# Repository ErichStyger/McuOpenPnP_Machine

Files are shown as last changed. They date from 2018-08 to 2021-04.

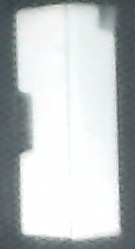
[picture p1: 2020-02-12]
CHM36VA_OpenPnP/V2/org.openpnp.machine.reference.feeder.ReferenceDragFeeder.Vision/tmpl_2714184057134874055.png

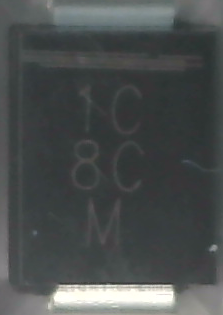
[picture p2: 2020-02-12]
CHM36VA_OpenPnP/V2/org.openpnp.machine.reference.feeder.ReferenceDragFeeder.Vision/tmpl_781869377021545644.png

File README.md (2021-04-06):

# McuOpenPnP_Machine
Repository for the McuOnEclipse OpenPnP machine.

The AutoFeeder is a contribution from Simon Huber (https://github.com/Scavenger18/RepoPNP) (many thanks!).

You can find overview videos about it on YouTube:
- Pick&Place Maschine Overview (Embedded Computing Conference 2018 Talk): https://youtu.be/OPd62hStLSc
- Pick&Place OpenPnP Overview (Embedded Computing Conference 2018 Talk): https://youtu.be/8GyD9tZBJVQ
- Placing SMD Resistors with OpenPnP Pick&Place machine: https://youtu.be/lebx-vkmo2o
- OpenPnP Pick&Place Component Iteration: https://youtu.be/lf4krekVuLk
- OpenPnP and Board Fiducials: https://youtu.be/fgSJTeFeqYE
- Nozzle Change with OpenPnP: https://youtu.be/CIzX5zvgmOw
- CHM-T32VA OpenPnP Conversion: https://mcuoneclipse.com/2020/05/03/retrofitting-a-charmhigh-chm-t36va-machine-with-openpnp/

And check out my blog articles on OpenPnP: https://mcuoneclipse.com/tag/openpnp/

Enjoy!

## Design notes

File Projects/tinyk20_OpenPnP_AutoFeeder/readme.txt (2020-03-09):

readme.txt
----------
Project for an OpenPnP Feeder using Kinetis Design Studio V3.2.0.

Links:
https://mcuoneclipse.com/2018/05/05/sneak-preview-diy-smt-pick-place-machine-with-openpnp/
https://mcuoneclipse.com/2018/06/26/building-a-diy-smt-pickplace-machine-with-openpnp/
https://mcuoneclipse.com/2018/06/03/embedded-computing-conference-2018-pickplace-overview-video/
https://mcuoneclipse.com/2018/03/18/3d-printed-smt-cut-tape-holder/
https://mcuoneclipse.com/2019/11/26/openpnp-solder-paste-dispensing-video/
https://mcuoneclipse.com/2019/08/15/openpnp-solder-dispenser-sneak-preview/

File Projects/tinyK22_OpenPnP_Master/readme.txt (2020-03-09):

readme.txt
----------

This project implements a sub driver for an OpenPnP (www.openpnp.org) pick and place machine, using Kinetis Design Studio 3.2.0.

USB, RTT and UART (over USB with AS1) are used to communicate with the host.
AS2 is used as UART connection to the OpenPnP feeders.

Links:
https://mcuoneclipse.com/2018/05/05/sneak-preview-diy-smt-pick-place-machine-with-openpnp/
https://mcuoneclipse.com/2018/06/26/building-a-diy-smt-pickplace-machine-with-openpnp/
https://mcuoneclipse.com/2018/06/03/embedded-computing-conference-2018-pickplace-overview-video/
https://mcuoneclipse.com/2018/03/18/3d-printed-smt-cut-tape-holder/
https://mcuoneclipse.com/2019/11/26/openpnp-solder-paste-dispensing-video/
https://mcuoneclipse.com/2019/08/15/openpnp-solder-dispenser-sneak-preview/

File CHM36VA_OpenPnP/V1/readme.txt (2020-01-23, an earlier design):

machine configuration files for the CHM36VA with OpenPnP.

Commands:

Defaults:
	COMMAND_CONFIRM_REGEX	
		^ok.*
	CONNECT_COMMAND
		G21 ; Set millimeters mode
		G90 ; Set absolute positioning mode
		M82 ; Set absolute mode for extruder
	HOME_COMMAND
		G28 ; Home all axes
	MOVE_TO_COMMAND
		G0 {X:X%.4f} {Y:Y%.4f} {Z:Z%.4f} {Rotation:E%.4f} F{FeedRate:%.0f} ; Send standard Gcode move
		M400 ; Wait for moves to complete before returning

VAC
	ACTUATE_BOOLEAN_COMMAND		M80{True:8}{False:9} ; M808/809

BLOW
	ACTUATE_BOOLEAN_COMMAND		M81{True:2}{False:3} ; M812/813

UPLED
	ACTUATE_BOOLEAN_COMMAND		M81{True:0}{False:1} ; M810/811
	ACTUATE_DOUBLE_COMMAND		M810 S{IntegerValue}

DOWNLED
	ACTUATE_BOOLEAN_COMMAND		M81{True:4}{False:5} ; M814/815
	ACTUATE_DOUBLE_COMMAND		M814 S{IntegerValue}		

CAMSW (not used any more)
	ACTUATE_BOOLEAN_COMMAND		M81{True:8}{False:9} ; M818/819	

RFEEDER
	ACTUATE_BOOLEAN_COMMAND		T3G92E0G0E5	

Head: N1 is left, N2 is right

H1:N1VSENSE	
	ACTUATOR_READ_COMMAND		M105 ; read temp
	ACTUATOR_READ_REGEX		^ok V1:(?<Value>\d+\.\d+) /0.0 @0 V2:(?<n2vsense>\d+\.\d+) /0.0 @0
H1:N2VSENSE
	ACTUATOR_READ_COMMAND		M105 ; read temp
	ACTUATOR_READ_REGEX		^ok V1:(?<n1vsense>\d+\.\d+) /0.0 @0 V2:(?<Value>\d+\.\d+) /0.0 @0

H1:N1VAC	N1 vaccuum on/off
	ACTUATE_BOOLEAN_COMMAND		M80{True:0}{False:1} ; M800/801

H1:N2VAC	N2 vaccuum on/off
	ACTUATE_BOOLEAN_COMMAND		M80{True:4}{False:5} ; M804/805

H1:DRAGPIN (caution: do not enable it for more than a second, otherwise it will be damaged!)
	ACTUATE_BOOLEAN_COMMAND		
		M81{True:6}{False:7} ; M816/817
		G4P50 ; 100ms delay to deploy/retract
	ACTUATOR_READ_COMMAND		M119 ; endstop status
	ACTUATOR_READ_REGEX		^X_min:\d Y_min:\d Z_min:\d pins- \(X\)P\d.\d+:\d \(Y\)P\d.\d+:\d \(Z\)P\d.\d+:\d \(Z\)P\d.\d+:(?<Value>\d)

H1:ZMIN
	ACTUATOR_READ_COMMAND		M119 ; endstop status
	ACTUATOR_READ_REGEX		^X_min:\d Y_min:\d Z_min:\d pins- \(X\)P\d.\d+:\d \(Y\)P\d.\d+:\d \(Z\)P\d.\d+:(?<Value>\d) \(Z\)P\d.\d+:\d

H1:LFEEDER
	ACTUATE_BOOLEAN_COMMAND		T2G92E0G0E5

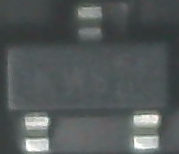
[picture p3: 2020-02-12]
CHM36VA_OpenPnP/V2/org.openpnp.machine.reference.feeder.ReferenceDragFeeder.Vision/tmpl_8623262849887002357.png

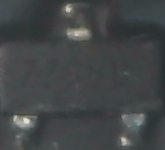
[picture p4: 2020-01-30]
CHM36VA_OpenPnP/V2/org.openpnp.machine.reference.feeder.ReferenceDragFeeder.Vision/tmpl_7061659952518420808.png

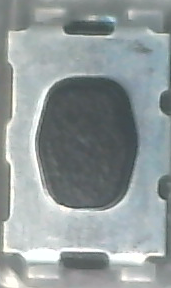
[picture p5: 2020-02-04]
CHM36VA_OpenPnP/V2/org.openpnp.machine.reference.feeder.ReferenceDragFeeder.Vision/tmpl_8939954195139066823.png

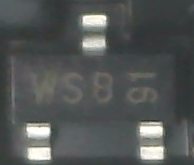
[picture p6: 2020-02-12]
CHM36VA_OpenPnP/V2/org.openpnp.machine.reference.feeder.ReferenceDragFeeder.Vision/tmpl_3286097203758662613.png

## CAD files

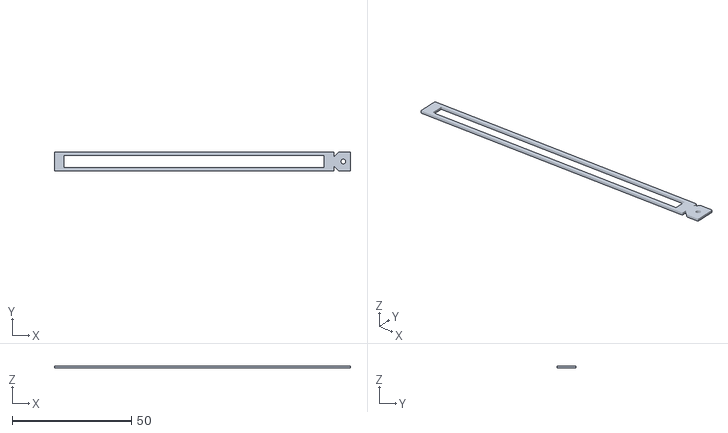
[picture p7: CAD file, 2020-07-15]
3D/StripFeeders.stl
124.0 x 8.00 x 1.00

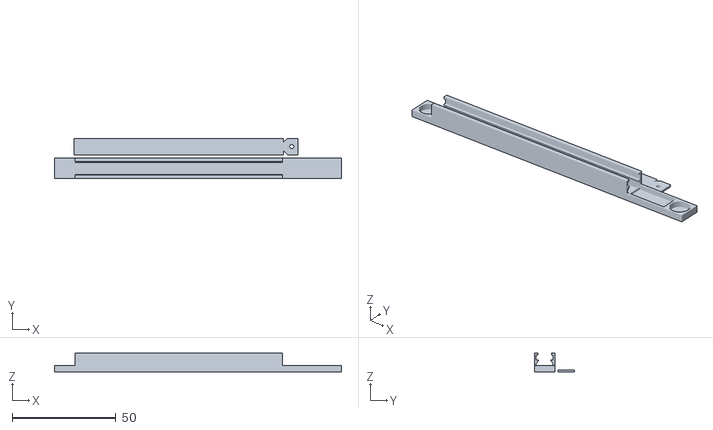
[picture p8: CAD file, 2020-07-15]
3D/StripFeederBase.stl
138.5 x 19.5 x 9.00

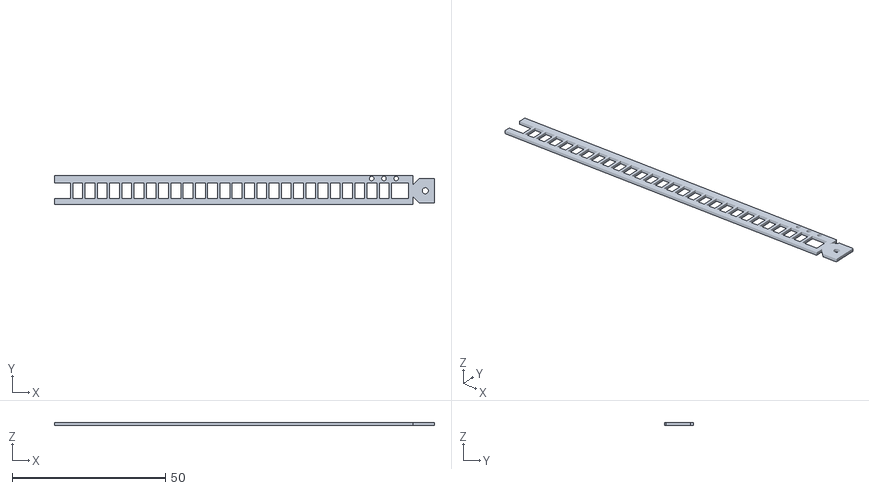
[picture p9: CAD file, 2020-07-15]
3D/feederTransparent.stl
124.0 x 9.50 x 1.00

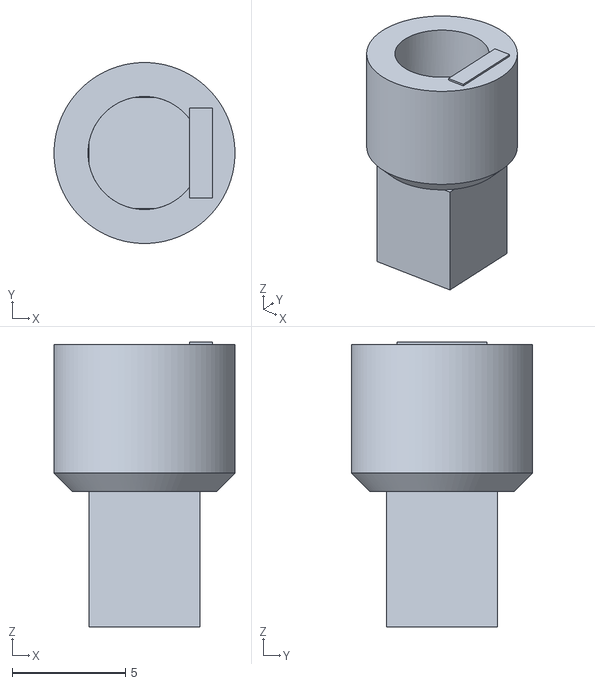
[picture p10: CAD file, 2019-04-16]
3D/SolderDispenser.stl
8.00 x 8.00 x 12.6

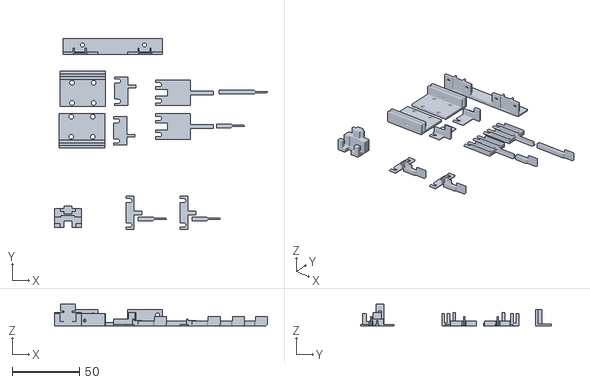
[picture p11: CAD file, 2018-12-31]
3D/Endstop.stl
158.0 x 141.9 x 16.0

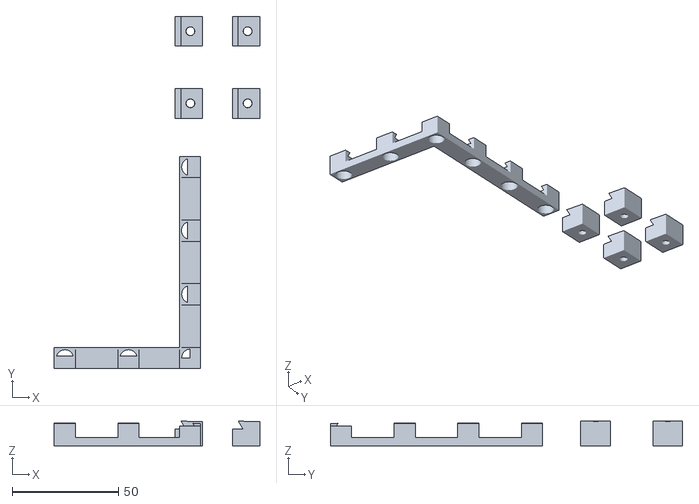
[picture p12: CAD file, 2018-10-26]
3D/PCBHolder.stl
97.0 x 166.0 x 11.7

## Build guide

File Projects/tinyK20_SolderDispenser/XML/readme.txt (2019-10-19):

This folder contains example OpenPnP configuration which is used for solder dispensing.

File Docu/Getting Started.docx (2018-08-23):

# Pick&Place: Getting Started

This document shall get you started on the McuOnEclipse OpenPnP machine. It is a quick and rough guide and will be enhanced and improved over time, so any feedback is more than welcome! This document will be available on GitHub/Wiki hopefully soon.

## Links and documents

- OpenPnP: http://openpnp.org/
- Blog: https://mcuoneclipse.com/2018/06/26/building-a-diy-smt-pickplace-machine-with-openpnp/
- Blog: https://mcuoneclipse.com/2018/05/05/sneak-preview-diy-smt-pick-place-machine-with-openpnp/
- GitHub: https://github.com/ErichStyger/McuOpenPnP_Machine

## Software

The following version is used: 2018-07-02. There is a newer version available, but has NOT been tested yet.

The software is available from: http://openpnp.org/downloads/

## USB Ports

You need two USB ports on the host. It is not possible to use two cameras on the same USB port/hub).

With the two USB cables (down camera and Smoothie board) plugged in).

You should have 3 USB ports:

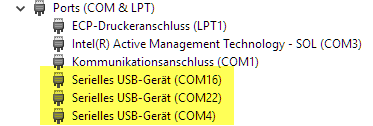
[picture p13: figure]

The port numbers depend on your machine.

Two ports are to the Smoothie board at 115200 baud (type ‘help’). One port will be used by OpenPnP, the other is available for a console connection in parallel.

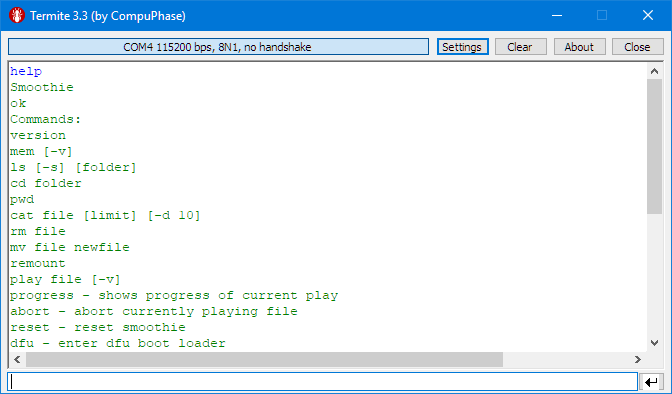
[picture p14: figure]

Another is the tinyK22 which is the master for the motorized feeders:

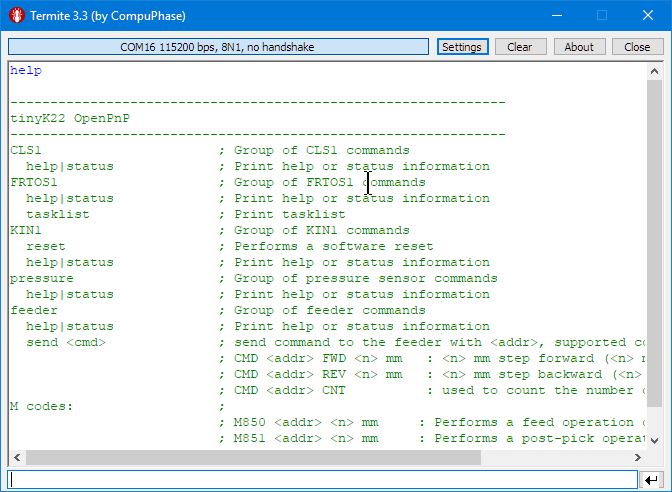
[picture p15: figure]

Remember your port numbers.

With both USB cables plugged in, two cameras shall show up:

## Machine Configuration

Start OpenPnP, then go to the Scripts Directory:

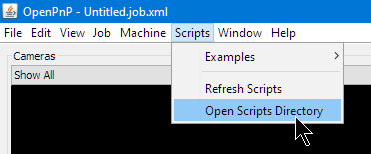
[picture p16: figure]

Go one directory up:

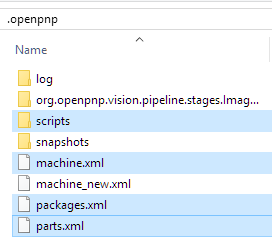
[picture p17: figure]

Exit OpenPnP (important, otherwise your files copied below might be overwritten, as OpenPnP updates the files on exit).

Replace the files with the ones from GitHub:

https://github.com/ErichStyger/McuOpenPnP_Machine/tree/master/OpenPnP

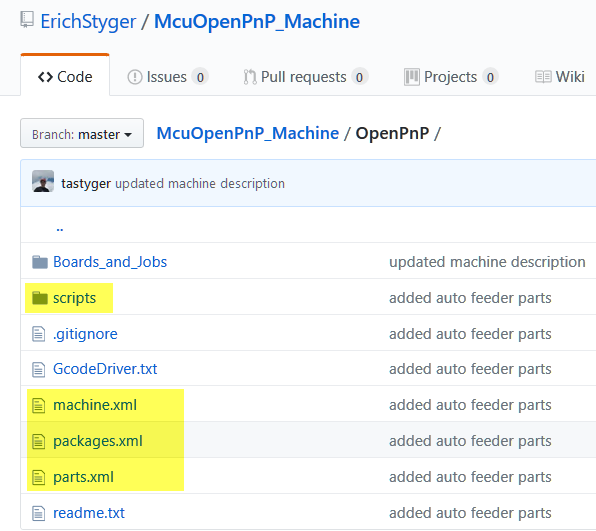
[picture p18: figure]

## Machine Setup (Ports)

Use the port to the Smoothie for the GcodeDriver:

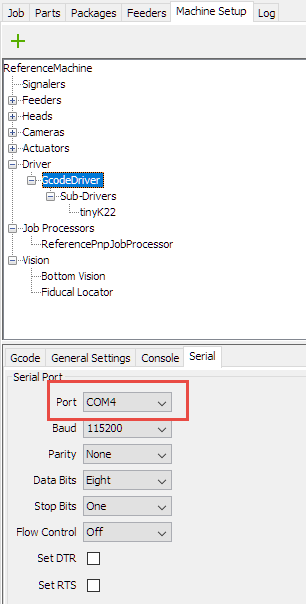
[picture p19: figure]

Use the port to the tinyK22 (motorized feeder):

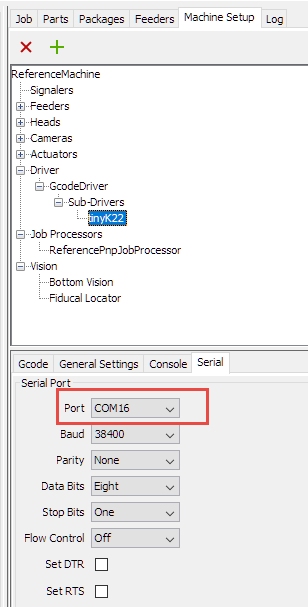
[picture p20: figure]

Camera is a bit tricky, as they show up with the same name. You might have to use the ‘first’ and the ‘second’ driver.

Head Camera:

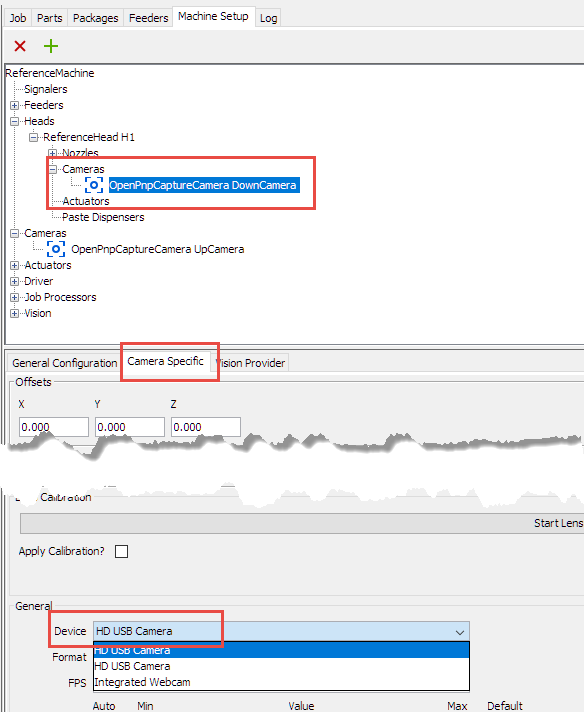
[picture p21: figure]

Up Camera:

Don’t forget to use the ‘Apply’ Button!

## Starting the Machine

1. Move the head to the origin (left upper corner) with both heads in the middle position (we don’t want a head crash later on)
2. First power the machine with the switch on the back of the power supply. The LCD display shows the X, Y and Z positions
3. Plug in the USB cables (otherwise the display might not show up properly)
4. Start OpenPnP Software

## Machine Alignment

The X axis is driven by two stepper motors and need to be properly aligned.

Make sure the motors are not turned on in the machine.

Move the head to the left:

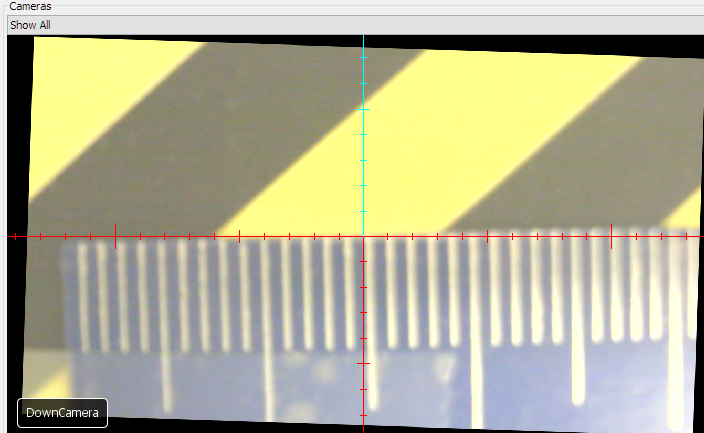
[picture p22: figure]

The move the head to the right. With the left belt fixed, move the right belt to have it correctly aligned. You might need to repeat that step once more.

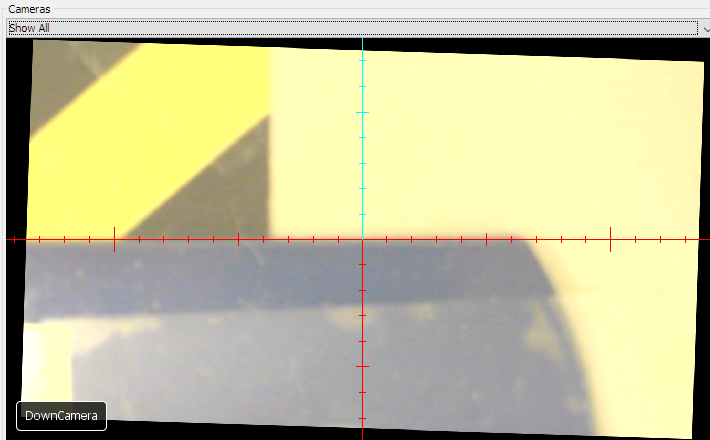
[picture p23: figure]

Move the head to the origin (top left) position and then turn it on.

Do a Homing:

If the home position is not in the center, repeat the homing.

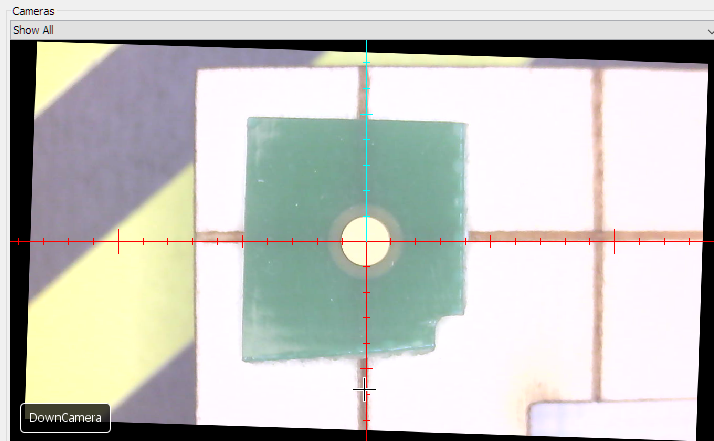
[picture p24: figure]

Do a Jogging to verify alignment:

If it is not perfectly aligned, turn off the machine and repeat.

## Nozzle-Camera Offset

If needed, the offset between nozzles and camera needs to be adjusted:

1. Mark the Nozzle position (e.g. using a piece of clay)
2. Click in the position field to zero it:
3. Move the camera to that marker and use the offset for the nozzle

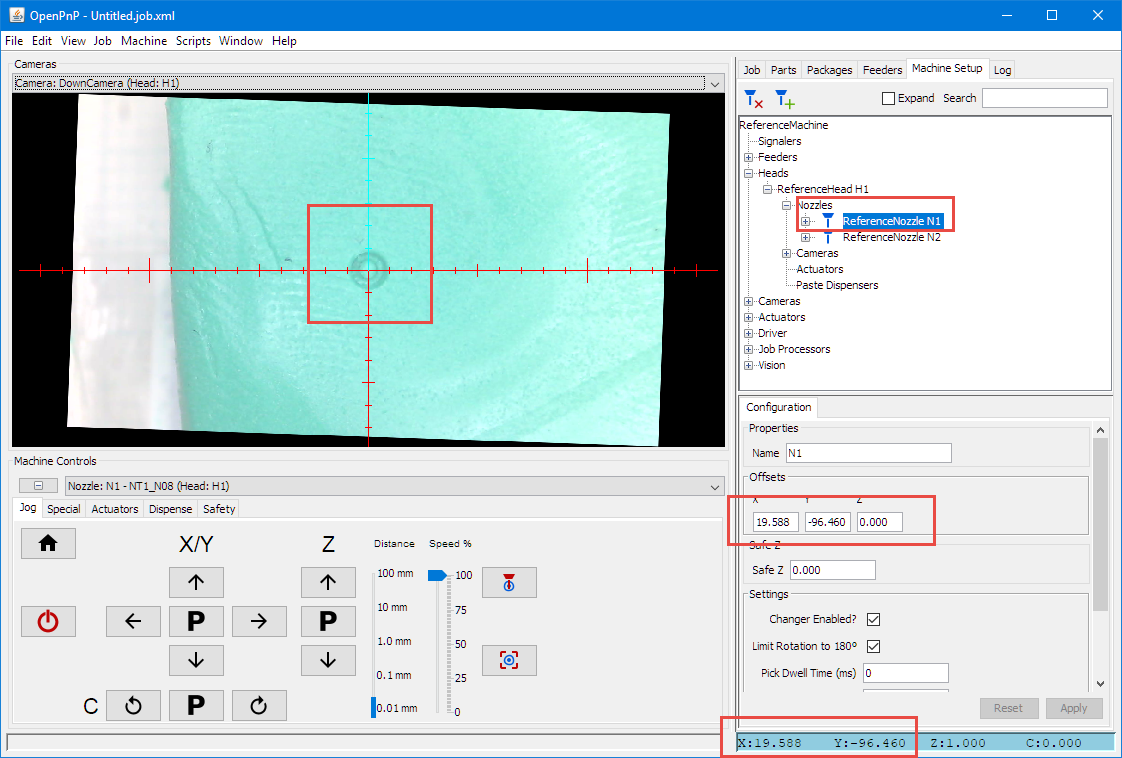
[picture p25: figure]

## Down Camera Position

Center both tools over the up-looking camera. They shall be centered, otherwise update camera position:

## Controls

The Jogging/Park (P) controls are for a given Camera or Nozzle (be careful not to do a head crash!)

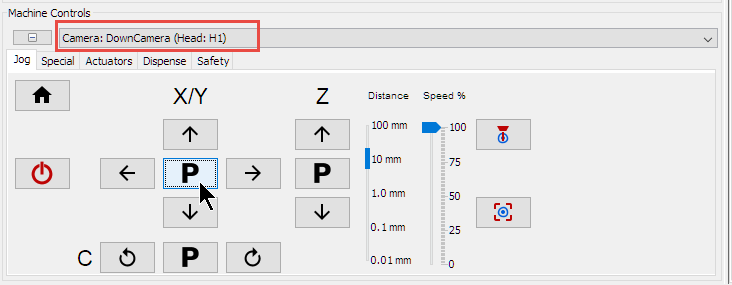
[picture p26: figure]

You can place the cursor with SHIFT pressed to move to a position

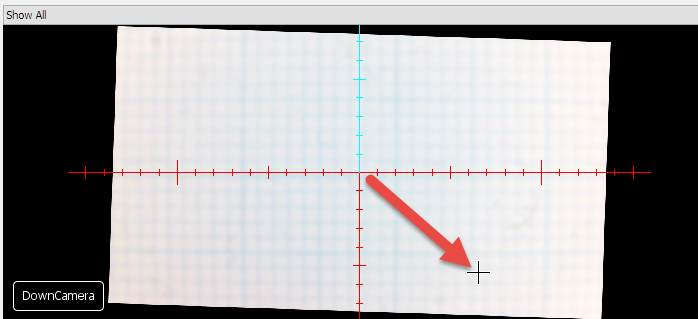
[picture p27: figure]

The ‘blue’ ones are used for capture a position (be careful, this can overwrite your settings!), and the red ones move the currently selected head/camera/nozzle (be careful not to produce a head crash!).

## KiCAD Placement Export

In KiCAD, export the position information:

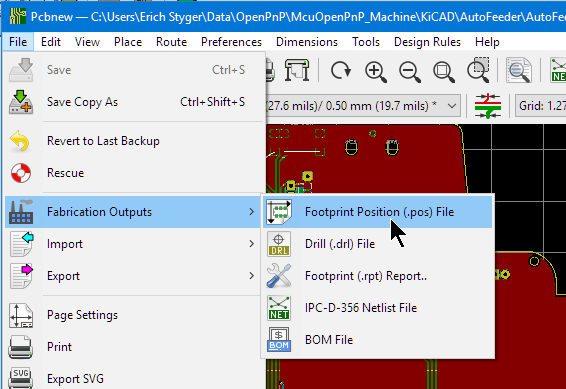
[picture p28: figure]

## New Job

Add new board (it will ask where to store the board settings):

Use CTRL-S to save the job anytime.

Specify board dimensions:

Jog with the head camera to the board (0,0) coordinate:

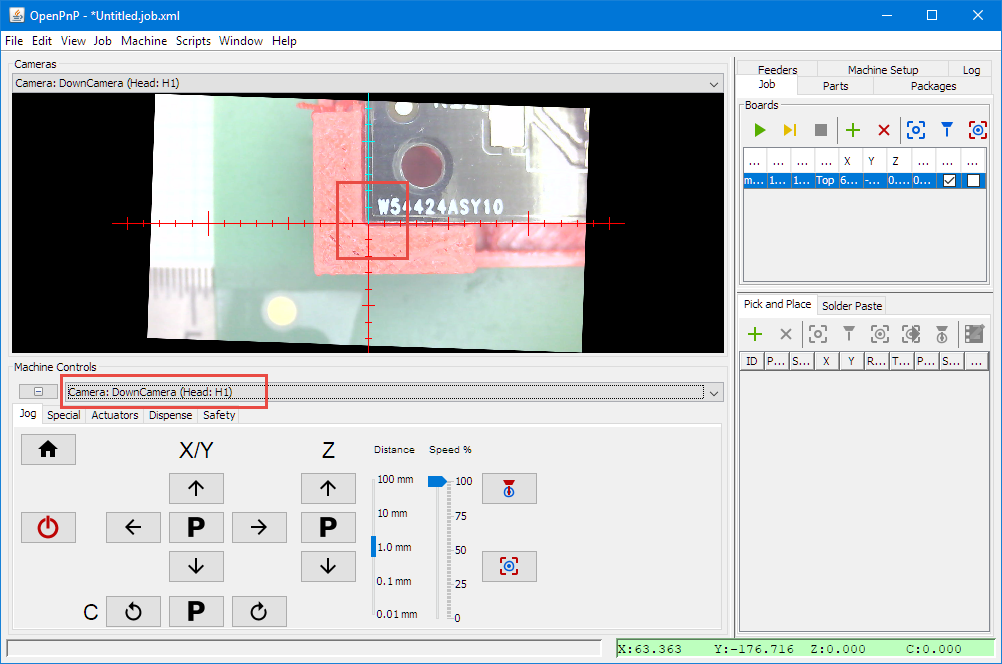
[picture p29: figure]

Use the button to store the coordinates:

Move the Nozzle to the board origin:

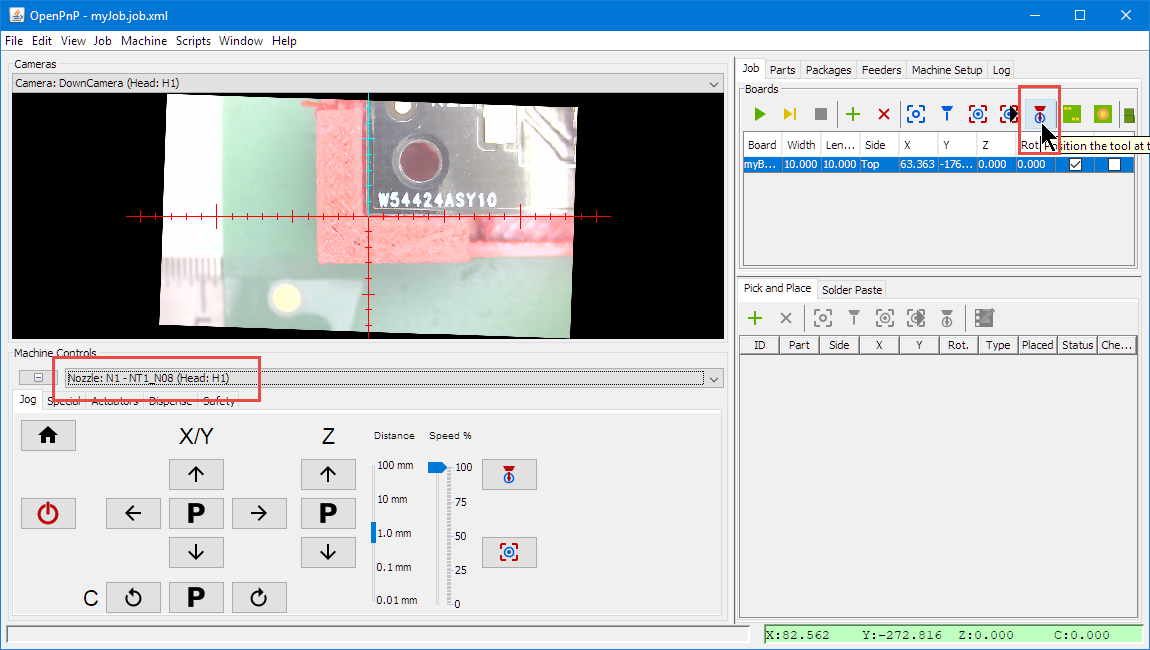
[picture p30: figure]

Lower the Nozzle to find the Z position of the board and enter it into the board information:

Rotation Axis of the board shall be minimal or zero:

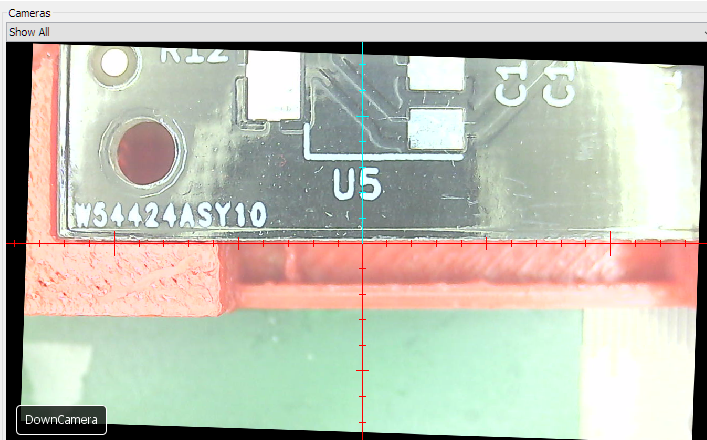
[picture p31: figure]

## Importing position information

Add the placement:

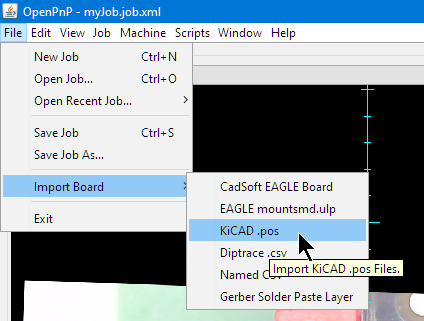
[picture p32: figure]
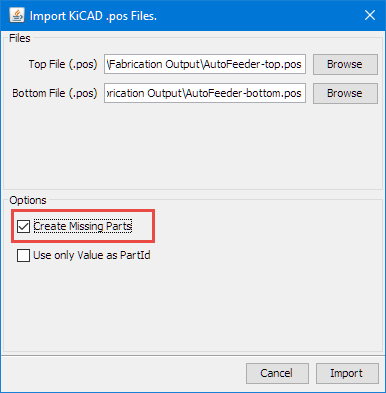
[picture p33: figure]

Assigning fiducials:

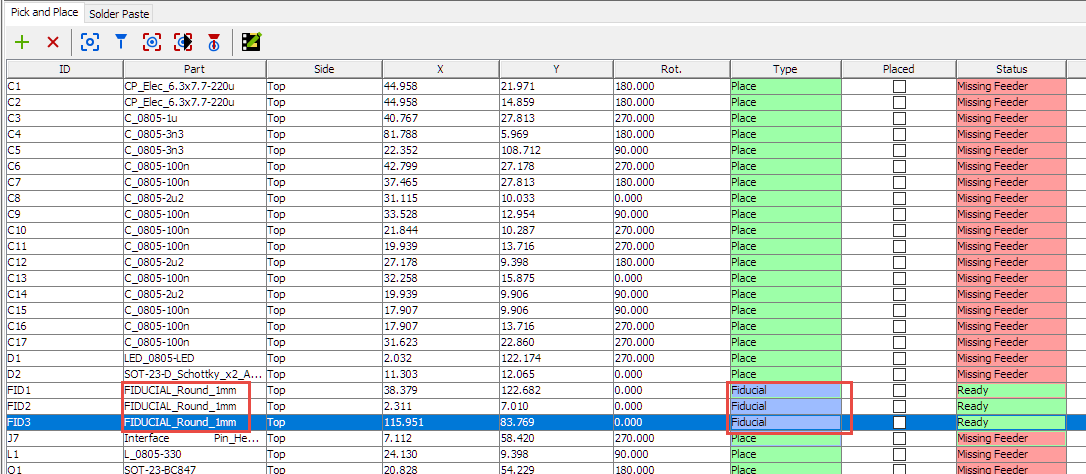
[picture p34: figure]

Test Fiducials (might set fiducials checks at start of job):

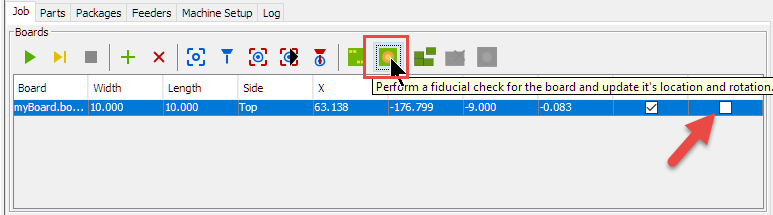
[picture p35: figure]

Assign Feeders or disable placing of parts.

#### Feeders

Move camera to strip feeder location:

Can perform an auto-setup:

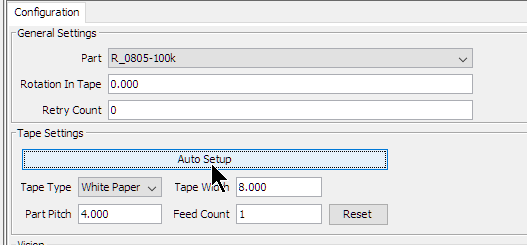
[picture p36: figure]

Green circles show detected holes:

Do not forget to press ‘Apply’.

Verify part position and location with the camera:

## End-Stops and Emergency Stop

In case of hitting the dnd stops or pushing the emergency stop push button:

1. Press and release emergency stop button (will unlock the Smoothie board again)
2. Make sure that the head is in a safe position
3. Home the machine again

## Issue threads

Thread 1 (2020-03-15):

Cannot import McuOpenPnP_Machine/Projects/tinyk20_OpenPnP_AutoFeeder/

duncanellison, 2020-03-15:
I'm trying to import the AutoFeeder project into KDS 3.2.0, but can't get a clean build.

What dependencies also need to be created to build this?

ErichStyger, 2020-03-15:
Have you downloaded and installed the McuOnEclipse Processor Expert components from https://sourceforge.net/projects/mcuoneclipse/?
See https://mcuoneclipse.com/2014/10/21/mcuoneclipse-releases-on-sourceforge/

duncanellison, 2020-03-15:
Yes, I installed the two beans packages and saw that the components were now available in the Eclipse PE section.  Latest seem to be 31-12-19, so that's what I used.

duncanellison, 2020-03-15:
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

ErichStyger, 2020-03-15:
The missing CPU.h and PE_Types.h indicates to me that code has not been generated? Do you have  folder Generated_Code with these files in it?

ErichStyger, 2020-03-15:
I see that third error (Generator Error): so your code generation was not sucessful. Did you load that project before you had installed the packages?

ErichStyger, 2020-03-15:
This is how it should look like:
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

duncanellison, 2020-03-15:
Hi Erich,  I loaded the PE components first, then imported the project, then tried to generate code and that was the result.  I just tried to generate the PE code again and now I have a (slightly) different result.  CPu.c is there, but not the header file :-(  and I'm looking at 2,222 errors now, mainly bad declaration errors.  I'll post a screenshot.   p.s. thanks for helping with this.

duncanellison, 2020-03-15:
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

duncanellison, 2020-03-15:
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

duncanellison, 2020-03-15:
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

ErichStyger, 2020-03-15:
Can you attach your .pe file (in the project root folder) so I can have a look?

duncanellison, 2020-03-15:
Here you go ...
[ProcessorExpert.pe.txt](https://github.com/ErichStyger/McuOpenPnP_Machine/files/4334946/ProcessorExpert.pe.txt)

ErichStyger, 2020-03-15:
thanks. That file works fine for me. Not sure what I'm missing, or if I have a change on my side which is not present on your end. Have you already restarted the IDE?

duncanellison, 2020-03-15:
Yes, I tried restarting the IDE , then a build - same result.  Tried regenerating  the PE code - no warnings, but still won't build.

I'm getting a ton of this stuff in the console

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

ErichStyger, 2020-03-15:
it looks like it did not properly generate all the needed files. Strange. And you are using KDS 3.2.0, correct?

duncanellison, 2020-03-15:
Correct KDS 3.2.0 direct from from the NXP site.

If it helps, here's an archive of the project
[non-working.zip](https://github.com/ErichStyger/McuOpenPnP_Machine/files/4334991/non-working.zip)

ErichStyger, 2020-03-15:
Here is what I have (with generated files) on my machine:
[tinyk20_OpenPnP_AutoFeeder.zip.txt](https://github.com/ErichStyger/McuOpenPnP_Machine/files/4334992/tinyk20_OpenPnP_AutoFeeder.zip.txt)

duncanellison, 2020-03-15:
OK, Thanks - let me try importing that

ErichStyger, 2020-03-15:
I believe it is about a fix I have made in the components. I get the errors if I compile your files. But it works fine if I regenerate the code. Give me a bit of time to generate the components package for you.

duncanellison, 2020-03-15:
OK, that DOES build (withing the same IDE environment) and gives me an .elf file.  Hmmm ...  now I'm left wondering what was missing before.

BTW (caution - thread drift) - I see there is activity on this project and you dropped an .srec file onto the repo.  How are you converting the .elf to .srec?

ErichStyger, 2020-03-15:
Can you try with the attached components?
[Components_15.03.2020.zip.txt](https://github.com/ErichStyger/McuOpenPnP_Machine/files/4335009/Components_15.03.2020.zip.txt)

ErichStyger, 2020-03-15:
Note: I checked the differences in the generated files, but there was nothing really hitting my eye. What is strange that your generated code somehow does not know about the standard types like int8_t or int32_t somehow. Strange.

ErichStyger, 2020-03-15:
.srec: it is an option in the 'Toolchains' tab, see https://mcuoneclipse.com/2014/04/11/gnu-additional-tools-create-flash-image-print-size-and-extended-listing-options/

duncanellison, 2020-03-15:
re : Srec - great that's handy for J-Flash Lite

duncanellison, 2020-03-15:
Update : with the updated PE components, same result - doesn't build.

With the generated code you sent, I can compile, build and debug 100%.  Made changes to the code and they were reflected in the object sent to the uC.

Got to rush off now, but I'll investigate a little further tomorrow what the differences might be.  Clearly the build environment is OK since it can compile and build your code version properly, so it must be in the PC components somehow.

Thanks for you help on this - worst case, I can use your build to debug an issue I'm having with the motor drive which requires me to add some debug code.

ErichStyger, 2020-03-16:
ok, so this means it is not about the components. I noticed that the Processor Expert (core) for you generated slightly different things (comment headers). Could you check what you have installed? Below is what I have:
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

duncanellison, 2020-03-16:
I have just the same  ...

duncanellison, 2020-03-16:
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

duncanellison, 2020-03-16:
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

duncanellison, 2020-03-16:
I'm happy to report no issues at all with the project pack you sent me above within the same environment - odd.

ErichStyger, 2020-03-16:
yes, this is odd. I'm going to close the issue, simply re-open if you think it is appropriate.

CircuitSetup, 2020-03-16:
FWIW, I just loaded everything up and it built without issue.

duncanellison, 2020-03-19:
Hi Erich,

I can confirm that if I load the project from the file you gave above, plus the updated components, I can do a clean compile right out of the gate as others are reporting.

However ...  If I run Project > Generate Processor Expert Code then try to build, it breaks, throwing out all the undefined types errors we discussed earlier.

Tried deleting the Generated_Code and Static_code folders to let them re-generate completely, then tried again, but this time I get a different failure mode with .h files missing

C:/Users/Duncan Ellison/kds_workspace.kds/tinyk20_OpenPnP_AutoFeeder/Generated_Code/BitIoLdd5.h:91:22: fatal error: GPIO_PDD.h: No such file or directory

C:/Users/Duncan Ellison/kds_workspace.kds/tinyk20_OpenPnP_AutoFeeder/Generated_Code/BitIoLdd1.h:94:22: fatal error: GPIO_PDD.h: No such file or directory

C:/Users/Duncan Ellison/kds_workspace.kds/tinyk20_OpenPnP_AutoFeeder/Generated_Code/BitIoLdd1.h:94:22: fatal error: GPIO_PDD.h: No such file or directory

I guess others are just aiming to get a build and create the .src / .hex and be done, but I'm trying to add some additional fault checking code to make assembly and maintenance easier (e.g. run 90 steps and check each hole is clear)

I can manage since I can compile the code if I don't mess with the components, but its frustrating no knowing what's causing this.  Like I said I'm a newbie at Processor Expert, but I think this is the way it should work and keen to be able to add to this project.

Duncan

duncanellison, 2020-03-19:
p.s.  The Master project is the other way round.  It doesn't build unless I DO re-generate the PE, then it builds fine, this leads me to think that my build environment is fine and the components.

ErichStyger, 2020-03-20:
The GPIO_PDD.h is iniside Static_Code/PDD and is only generated at project creation time, not at build or code generation time. If it does not find it on your machine, it means that it has been deleted? Strange.
As for the masters project: after importing it from git, you have to generate code (either manually or automatically) because the generated code is not part of the Git repo, because usually generated code shall not be on a source repository.

I think I will now put the generated code on git too: that way there is always a working version and there is no need to generate code.

Closed 2020-03-16.

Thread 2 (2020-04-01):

Tape motor not moving with OpenPnp M850

CircuitSetup, 2020-04-01:
The tape motor appears to work like it should with the on-board buttons, but does not move with an M850 command from OpenPnp.

I see in the code where MOT_Speed is used for the buttons to control the tape motor, but am not seeing the same function where M850 is handled in comm.c (or m851). It doesnt matter if the tape cover switch is depressed or not. Maybe I'm missing something?

ErichStyger, 2020-04-02:
I'm a bit in crunch right now, but I will look into this in the next days.

duncanellison, 2020-04-02:
Erich, just to advise that I'm seeing the exact same issue too.  Pushing the buttons works 100% as expected, so there's no hardware issues here.

I kind of expected the tape motor code to be on a separate free running thread taking care of itself, but I don't see anything like that in the code.

Your assistance would be much appreciated.

ErichStyger, 2020-04-02:
ok, thanks for confirming. I don't have the hardware with me because of Corona and the university closure. I have to see if I can access the hardware and try it out on my side, but it will take me until the weekend to get there.

duncanellison, 2020-04-02:
Hi Erich,  we are most grateful to you for your help.   We don't mind poking around in the code and trying to debug physically this if you could give us some steerage on where to look.  I don't think either of us are FreeRTOS experts, but we might even learn something :-)

We both have pretty identical hardware and can try out any changes.  Our biggest challenge is that we can't find the code that's supposed to work the tape feeder under serial command.

BTW, I can confirm that it's not specifically an 'M850' problem as I'm sending the raw serial command to mine with the same result.

It feels like we are both missing something really obvious.

ErichStyger, 2020-04-06:
The M850 command is received by the Master board (a tinyK22 (K22FN512), you can see it inhttps://mcuoneclipse.files.wordpress.com/2018/06/tinyk22.png?w=584&h=493) and handled in https://github.com/ErichStyger/McuOpenPnP_Machine/blob/master/Projects/tinyK22_OpenPnP_Master/Sources/Feeder.c
same for the M851 command.

`  } else if (UTIL1_strncmp((char*)cmd, "M850 ", sizeof("M850 ")-1)==0) { /* feed operation: "M850 <addr> <n> mm  */
    *handled = TRUE;

    p = cmd + sizeof("M850 ")-1;
    res = UTIL1_xatoi(&p, &addr);
    if (res==ERR_OK) {
      res = UTIL1_xatoi(&p, &mm);
      if (res==ERR_OK) {
        UTIL1_strcpy(buf, sizeof(buf), "CMD ");
        UTIL1_strcatNum32s(buf, sizeof(buf), addr);
        UTIL1_strcat(buf, sizeof(buf), " FWD ");
        UTIL1_strcatNum32s(buf, sizeof(buf), mm);
        UTIL1_strcat(buf, sizeof(buf), " mm");
        return FEED_SendCommand(buf, io);
      }
    }
  } else if (UTIL1_strncmp((char*)cmd, "M851 ", sizeof("M851 ")-1)==0) { /* post-pick operation: "M851 <addr> <n> mm  */
    *handled = TRUE;
    /* We are not doing anything right now. Print 'ok' message so it can be parsed by OpenPnP Regular Expression */
    CLS1_SendStr("ok\r\nok\r\nok\r\n", io->stdOut);
  }
`
So the OpenPnP M850 command gets translated into a CMD x FW command to the feeder. This command is supported by the feeder:

`--------------------------------------------------------------
TinyK20 OpenPnP Feeder
--------------------------------------------------------------
CLS1                      ; Group of CLS1 commands
  help|status             ; Print help or status information
KIN1                      ; Group of KIN1 commands
  reset                   ; Performs a software reset
  help|status             ; Print help or status information
CMD                       ; Group of CMD commands
  help|status             ; Print help or status information
  0 FWD <n> mm            ; Move feeder <n> mm forward (multiple of 2)
  0 REV <n> mm            ; Move feeder <n> mm backward (multiple of 2)
  0 CNT                   ; Count number of feeders
`

I hope that makes sense now?

CircuitSetup, 2020-04-06:
Thanks @ErichStyger. Right, that makes sense.

@duncanellison actually added some code to encoder.c to handle the tape pull motor that seems to have fixed the issue. It's similar that what is in Application.c for the FWD button.

Closed 2020-05-10.

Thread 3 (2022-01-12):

Lasercutter files

lucalutz2005-dev, 2022-01-12:
Hello,
first I want to thank you for sharing your project with the OpenSource community. But I was wondering if you may want to share your Lasercut files like in the following blog post (https://mcuoneclipse.com/2018/06/26/building-a-diy-smt-pickplace-machine-with-openpnp/).
Thank your already for answering this "Issue"

ErichStyger, 2022-01-12:
they are inside the 'Inkscape' folder of this repository.

Closed 2022-01-12.

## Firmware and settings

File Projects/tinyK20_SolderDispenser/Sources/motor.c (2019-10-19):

#include "platform.h"
#include "UTIL1.h"
#include "motor.h"
#include "wait1.h"
#include "step.h"
#include "led1.h"
#include "comm.h"
#include "cls1.h"
#include "MotEn.h"
#include "MotSleep.h"
#include "FRTOS1.h"
#include "MS1.h"
#include "MS2.h"
#include "Dir.h"
#include "WAIT1.h"
#include "platform.h"
#include "stdlib.h"

static MOT_state_t MOTstate;
static TaskHandle_t MotTaskHandle;

/* ===================================================================
 * - TASK NOTIFICATION
 * -------------------------------------------------------------------
 * the motor task can be notified as followed:
 *
 * MOT_START_CONTINUOUS:	starts the continuous dispensing mode
 * MOT_STOP_CONTINUOUS:		stops the continuous dispensing mode
 * MOT_SINGLE_DISP:			dispense a predefined amount
 *
 */

#define MOT_START_CONTINUOUS (1<<0)
#define MOT_STOP_CONTINUOUS (1<<1)
#define MOT_SINGLE_DISP (1<<2)

void MOT_StartContinuous(void) {xTaskNotify(MotTaskHandle, MOT_START_CONTINUOUS, eSetBits);}
void MOT_StopContinuous(void) {xTaskNotify(MotTaskHandle, MOT_STOP_CONTINUOUS, eSetBits);}
void MOT_SingleDisp(void) {xTaskNotify(MotTaskHandle, MOT_SINGLE_DISP, eSetBits);}

/* ===================================================================
 * - MOTOR DRIVER
 * -------------------------------------------------------------------
 * the motor can be controlled with the following funtions
 *
 * MOT_enable:		enables the motor driver
 * MOT_disable:		disables the motor driver
 * MOT_sleep:		disables the motor drivers output
 * MOT_wakeup:		ennables the motor drivers output
 * MOT_setMS:		the microstepping gets set by parameter
 * MOT_setDir:		the motor direction gets set by parameter
 *
 */

static void MOT_enable(void){
	EnterCritical();
	MotEn_ClrVal();
	ExitCritical();
	//SHELL_SendString("motor enabled\r\n");
}

static void MOT_disable(void){
	EnterCritical();
	MotEn_SetVal();
	ExitCritical();
	//SHELL_SendString("motor disabled\r\n");
}

static void MOT_sleep(void){
	EnterCritical();
	MotSleep_ClrVal();
	ExitCritical();
	//SHELL_SendString("motor sleeping\r\n");
}

static void MOT_wakeup(void){
	EnterCritical();
	MotSleep_SetVal();
	ExitCritical();
	//SHELL_SendString("motor woke up\r\n");
}

static void MOT_setMS(MicroStep_t ms){
	switch (ms) {
		case FULLSTEP:
			EnterCritical();
			MS1_ClrVal();
			MS2_ClrVal();
			MOTstate.MS = FULLSTEP;
			ExitCritical();
			//SHELL_SendString("fullstep\r\n");	// for debugging
			break;
		case HALFSTEP:
			EnterCritical();
			MS1_SetVal();
			MS2_ClrVal();
			MOTstate.MS = HALFSTEP;
			ExitCritical();
			//SHELL_SendString("halfstep\r\n");	// for debugging
			break;
		case STEP_1_4:
			EnterCritical();
			MS1_ClrVal();
			MS2_SetVal();
			MOTstate.MS = STEP_1_4;
			ExitCritical();
			//SHELL_SendString("1/4 step\r\n");	// for debugging
			break;
		case STEP_1_8:
			EnterCritical();
			MS1_SetVal();
			MS2_SetVal();
			MOTstate.MS = STEP_1_8;
			ExitCritical();
			//SHELL_SendString("1/8 step\r\n");	// for debugging
			break;
		default:
			break;
	}
}

static void MOT_setDir(MotDirection_t dir){
	switch (dir) {
		case UP:
			EnterCritical();
			MOTstate.MOT_DIR = UP;
			Dir_ClrVal();
			ExitCritical();
			//SHELL_SendString("direction up\r\n");	// for debugging
			break;
		case DOWN:
			EnterCritical();
			MOTstate.MOT_DIR = DOWN;
			Dir_SetVal();
			ExitCritical();
			//SHELL_SendString("direction down\r\n");	// for debugging
			break;
		default:
			break;
	}
}


/* ===================================================================
 * - MOTOR STATE METHODES
 * -------------------------------------------------------------------
 * the states of the motor can be modified as followed:
 *
 * MOT_setSteps:		saves the given amount of steps
 * MOT_getSteps:		returns the remaining steps
 * MOT_stepDone:		subtracts one step from the remaining steps
 * MOT_setContinuous:	sets the continuous dispensing mode flag
 * MOT_clearContinuous:	cleares the continuous dispensing mode flag
 * MOT_startDisp:		wakes the motor driver up and sets dispensing
 * 						flag to start the dispensing process
 * MOT_stopDisp:		clears the dispensing flag and puts the
 * 						motor driver to sleep
 *
 */

static void MOT_setSteps(int32_t steps){
	EnterCritical();
	MOTstate.STEPS = steps;
	ExitCritical();
	//SHELL_SendString("steps set\r\n");	// for debugging
}

static int32_t MOT_getSteps(void){
	EnterCritical();
	uint32_t steps =  MOTstate.STEPS;
	ExitCritical();
	return steps;
}

static void MOT_stepDone(void){
	EnterCritical();
	MOTstate.STEPS --;
	ExitCritical();
}

static void MOT_setContinuous(void){
	EnterCritical();
	MOTstate.CONTINUOUS = TRUE;
	ExitCritical();
	// SHELL_SendString("continuous set\r\n");	// for debugging
	SHELL_SendString("ok\r\n");
}

static void MOT_clearContinuous(void){
	EnterCritical();
	MOTstate.CONTINUOUS = FALSE;
	ExitCritical();
	// SHELL_SendString("continuous clear\r\n");	// for debugging
}

static void MOT_startDisp(void){
	MOT_wakeup();
	EnterCritical();
	MOTstate.DISPENSING = TRUE;
	ExitCritical();
	//SHELL_SendString("dispensing started\r\n");	// for debugging
}

static void MOT_stopDisp(void){
	EnterCritical();
	MOTstate.DISPENSING = FALSE;
	ExitCritical();
	//SHELL_SendString("dispensing stopped\r\n");	// for debugging
	SHELL_SendString("ok\r\n");
	MOT_sleep();
}

/* ===================================================================
 * - SHELL
 * -------------------------------------------------------------------
 * Communication and Commands:
 *
 * MOT_PrintHelp		prints defined commands for communication
 * MOT_PrintStatus		prints the current status of the system
 * MOT_ParseCommand		comparse and executes commands
 *
 */
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

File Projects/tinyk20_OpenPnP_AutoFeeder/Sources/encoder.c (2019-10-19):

/*
 * encoder.c
 *
 *  Created on: 25.03.2018
 *      Author: Simon Huber
 */
#include "platform.h"
#include "encoder.h"

#if PL_ENCODER_EN
#include "ENC1.h"
#include "CS1.h"
#include "FRTOS1.h"
#include "CLS1.h"
#include "motor.h"
#include "comm.h"

#define ENC_QUEUE_LENGTH    (10)
#define ENC_QUEUE_ITEM_SIZE (sizeof(int8_t))  /* -1 (backward) or 1 (forward) will be added for the steps */
static QueueHandle_t ENC_StepRequestQueue = NULL;

void ENC_RequestSteps(int8_t steps) {
  if (xQueueSendToBack(ENC_StepRequestQueue, &steps, portMAX_DELAY)!=pdPASS) {
    for(;;){} /* ups? */
  }
}

/*
 * calls status check of encoder
 * turns off sprocket motor accordingly
 */
static void ENC_task(void *param) {
  uint32_t err_cntr = 0;
	unsigned int enc_val = 0;
	int8_t steps;
  int32_t timeoutMs = 5000;

	(void)param;
	if (ENC1_GetVal()) { /* HIGH: sprocket wheel is not on a hole: move the sprocket with the motor to the hole */
	  COMM_SendStr("INFO: Initial sprocket move\r\n", FALSE);
	  MOT_Speed(MOT_SPROC, 100); /* turn on motor with 50% */
	  timeoutMs = 5000;
	  while(ENC1_GetVal()) {
	    vTaskDelay(pdMS_TO_TICKS(1)); /* wait until we reached to the hole */
      timeoutMs--;
      if (timeoutMs<0) {
        COMM_SendStr("ERROR: InitialSprocketMove\r\n", TRUE);
        break;
      }
	  }
	  MOT_Speed(MOT_SPROC, 0); /* turn off motor */
	  /* here the ENC1 should be LOW (light passes through the hole) */
	}
	for(;;) {
	  if (ENC1_GetVal()) { /* here the signal should be LOW (light goes through). If not, the wheel has moved? */
	    err_cntr++;
	  }
	  /* check if we get a semaphore to request a move */
	  if (xQueueReceive(ENC_StepRequestQueue, &steps, portMAX_DELAY)!=pdPASS) {
	    COMM_SendStr("blocked for semaphore, but got a timeout?\r\n", TRUE);
	  } else { /* received the semaphore, move sprocket motor */
	    while(steps!=0) {
	      timeoutMs = 5000;
        MOT_Speed(MOT_SPROC, steps>=0?100:-100); /* turn on motor  */
        while(!ENC1_GetVal()) { /* while signal is low and we are still over the hole */
          vTaskDelay(pdMS_TO_TICKS(1)); /* wait until the signal goes up and we passed the hole */
          timeoutMs--;
          if (timeoutMs<0) {
            COMM_SendStr("ERROR: StepForwardTapeFWTimeout\r\n", TRUE);
            break;
          }
        }
        /* now the signal is high (we are between holes: wait until the signal goes low again (we have reached the next hole) */
        timeoutMs = 5000;
        while(ENC1_GetVal()) {
          timeoutMs--;
          if (timeoutMs<0) {
            COMM_SendStr("ERROR: StepForwardTapeFWTimeout\r\n", TRUE);
            break;
          }
          vTaskDelay(pdMS_TO_TICKS(1)); /* wait until we reached to the hole */
        }
        /* now we reached the next hole */
        MOT_Speed(MOT_SPROC, 0); /* turn off motor */
        if (steps<0) {
          steps++;
        } else if (steps>0){
          steps--;
        }
	    }
	  }
		vTaskDelay(pdMS_TO_TICKS(1));
	} /* for */
}

/*
 * Initializes counters and flags
 * creates ENC Task
 */
void ENC_Init(void){
	ENC_StepRequestQueue = xQueueCreate(ENC_QUEUE_LENGTH, ENC_QUEUE_ITEM_SIZE);
  if (ENC_StepRequestQueue==NULL) {
    for(;;){} /* out of memory? */
  }
  vQueueAddToRegistry(ENC_StepRequestQueue, "EncStepReqQ");

  if (xTaskCreate(ENC_task, "ENC", 500/sizeof(StackType_t), NULL, tskIDLE_PRIORITY+2, NULL) != pdPASS) {
		for(;;){} /* error! probably out of memory */
	}
}

#endif

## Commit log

2018-08-22 added second nozzle changer
2018-09-25 carrier 2.5 mm wider for better stability.
2018-10-26 fixed PCB holder file (was wrong content in STL)
    [PCBHolder.stl]
2018-12-31 added all endstop parts
    [Endstop.stl]
2019-04-16 added new Auger pump adapter
    [SolderDispenser.stl]
2019-10-19 adding solder dispensing project
2020-01-22 added actuators
2020-01-23 removed simulated cameras
2020-01-27 added debug prints
2020-01-28 added runout calibration
2020-01-30 with first boards populated
2020-02-04 adde new feeders
    [StripFeeders.stl]
2020-02-04 changed feeder drag pin location
2020-02-04 used for producing the stepper clock boards
2020-02-12 completed APROG PCB
2020-02-14 added parts for the board from Chris
2020-02-15 updated machine after production run with 100 boards
2020-03-06 fixed nozzle ID
2020-03-09 enabling second nozzle
2020-03-09 fixed Y offset with setting a camera offset
2020-03-10 working 2nd nozzle
2020-04-07 updates after LED board production run
2020-04-07 using java.lang.Thread.sleep(500);
2020-06-22 new parts after doing PCB for Chris and new Clock2
2020-06-25 waiting more time after retracting the pull pin
2020-07-15 updated strip feeder
    [StripFeederBase.stl, StripFeeders.stl, feederTransparent.stl]
2020-07-15 updated machine config for building LED panel
